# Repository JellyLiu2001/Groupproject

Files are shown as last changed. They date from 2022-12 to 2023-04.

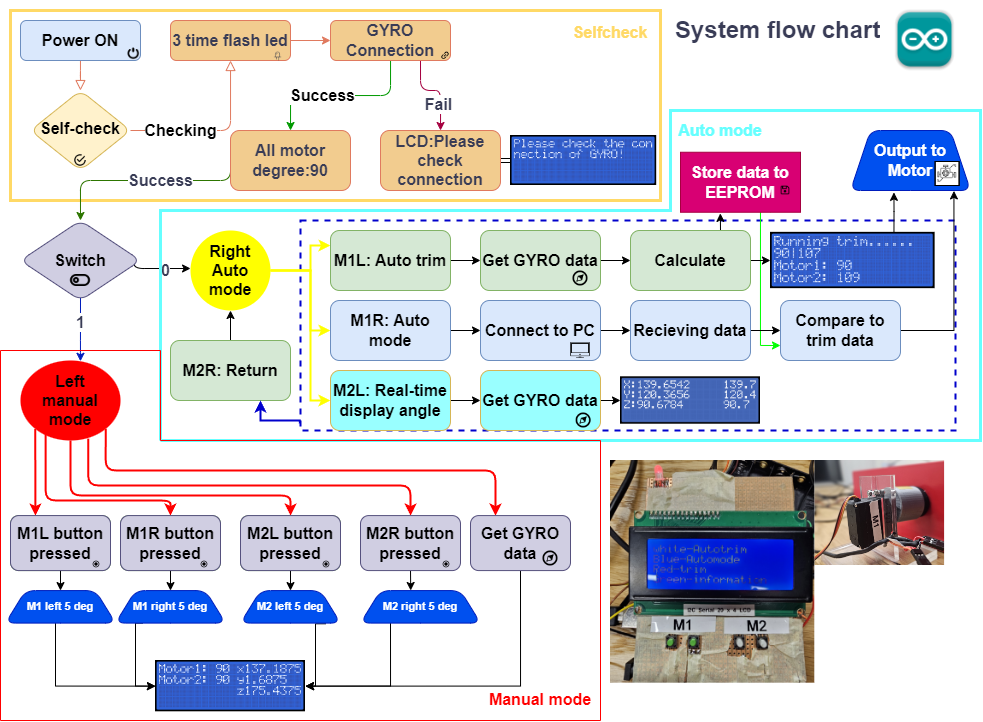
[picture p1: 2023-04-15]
Report-ab20328/flow chart.png

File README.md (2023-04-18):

# Groupproject
ab20328-Jelly Jinzhe Liu
## Abstract

This report is based on a group project of selecting and configuring motor and processor, designing a circuit, writing code, and discussing its feasibility.	
The part of this report on the group project is to discuss the feasibility of the motor and processor, using the result to choose the motor and integrated it into the maze. The processor needs to choose the model, design the circuits, and write the code. Also, when the image processing is finished, it must use the same port the processor provided. 

## Introduction
In the hardware part, the main function is using the motor to drive two knobs in the maze, which can control the pitch and roll. This function is leading the ball running in the guided route in case of not dropping the hole and to the destination. It uses two servo motors to drive the maze by connecting to Arduino Mega. when the system turns on, Arduino will do a self-check to make sure every component is connected and working well. Table 1 shows its component for users. 
After self-check, the user can choose two modes: auto mode and manual mode. It also includes auto trim, connect to pc and degree in auto mode. 
The benefit of this plan is to keep the original appearance and function of the maze, so people can still use it like the product itself. 

## Direction
Machines should always serve humans. A useful product not only has perfect hardware but also has good practicality. It is important to choose how to use it. 
In our design, the first task or main function is the connection to the PC and the use of two servos to drive the maze. Every part should give a visualization to the user to let them know what the system is doing, and easy to check errors. One of the problems is that the user will place the maze on different planes, therefore, the angle of the maze will change concerning the horizontal plane. In our design, we want it can be auto trim, which is to design a system that the user does not need to trim and still can get horizon. 
Config.h
Library	It is a set of pre-written code files designed to solve specific problems or provide specific functions, and developers can import them into their own code for use. A library can contain functions, variables, objects, etc., along with their associated header files, source code, and other resources.
adaFruint_sensor	Many small embedded systems exist to collect data from sensors, analyse the data, and either take an appropriate action or send that sensor data to another system for processing. (Adafruit, 2023)




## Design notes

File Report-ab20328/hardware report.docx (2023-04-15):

Jelly Jinzhe Liu – AB20328

AB20328@bristol.ac.uk

Mian contribution: Hardware

A clear report showing my contribution to the group project

Group Project 3 2022

Individual report

/

# Abstract

This report is based on a group project of selecting and configuring motor and processor, designing a circuit, writing code, and discussing its feasibility.

The part of this report on the group project is to discuss the feasibility of the motor and processor, using the result to choose the motor and integrated it into the maze. The processor needs to choose the model, design the circuits, and write the code. Also, when the image processing is finished, it must use the same port the processor provided.

# Introduction

Table 1 User’s component in Arduino mega
NAME | NUMBER
Button | 4
Switch | 1
LCD screen | 1
GYRO | 1
Full-colour LED | 1

In the hardware part, the main function is using the motor to drive two knobs in the maze, which can control the pitch and roll. This function is leading the ball running in the guided route in case of not dropping the hole and to the destination. It uses two servo motors to drive the maze by connecting to Arduino Mega. when the system turns on, Arduino will do a self-check to make sure every component is connected and working well. Table 1 shows its component for users.

After self-check, the user can choose two modes: auto mode and manual mode. It also includes auto trim, connect to pc and degree in auto mode.

The benefit of this plan is to keep the original appearance and function of the maze, so people can still use it like the product itself.

# Direction

Machines should always serve humans. A useful product not only has perfect hardware but also has good practicality. It is important to choose how to use it.

In our design, the first task or main function is the connection to the PC and the use of two servos to drive the maze. Every part should give a visualization to the user to let them know what the system is doing, and easy to check errors. One of the problems is that the user will place the maze on different planes, therefore, the angle of the maze will change concerning the horizontal plane. In our design, we want it can be auto trim, which is to design a system that the user does not need to trim and still can get horizon.

# Hypothesis/ Feasibility

## Motor/actuator

In this part, our main theme is trying to keep the product itself. Thus, we choose to use two knobs controlled by a servo motor.

The servo motor is a positional (angle) servo driver, which is suitable for the closed-loop control execution module that needs to change and maintain the angle constantly. In our project, we can be adjusting and monitor the angle by PWM. Compared to other motors, the servo motor has good stability and quick response. Therefore, I can control the knob fast and precisely.

Operating Speed: 60/0.15 degree/second (No Load @ 6.0V)

Stall Torque: 9.4 kg/cm @ 4.8V / Stall Torque: 11 kg/cm @ 6V

Running Current: 500mA-900mA @ 6V

Stall Current 2.5A @ 6v

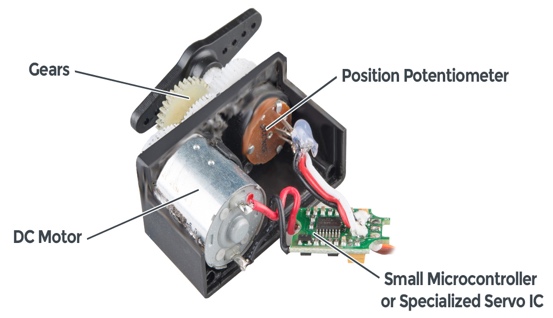
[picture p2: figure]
Servos Explained - SparkFun Electronics

Figure 1 - the structure of servo motor | Table 2 MG996R 180° servo motor features. (MG996R Servo Motor, 2019)

Figure 1 shows servo motor uses gears, which causes it can be high torque, and I can set the degree directly by using its potentiometer. In 6V, the torque can be 11kg/cm (Figure 1 - the structure of servo motor | Table 2 MG996R 180° servo motor features. (MG996R Servo Motor, 2019)). according to my measurement, the force of the knob is _____, Which is enough for our project. I did not choose a small servo motor, such as SG92R, So, I want to give some redundancy to prevent subsequent processes from adding weight.

## Processor

The processor’s main function is to drive two motors. It also should take part in connecting different hardware and transferring information. As I discussed with my group member, we will use the computer as the main computing service. Meanwhile, the hardware parts also need the ability to do some light work.

In this project, there are plenty of MCU (Microcontrollers unit) in the market, such as Arduino, Raspberry Pi and so on. As we considered, MCU does not participate in complex calculations. Thus, there is no need to use Raspberry Pi. Moreover, Arduino is our first choice.

### Choosing Arduino

According to the official website, Arduino is an open-source electric platform based on hardware and software. (Arduino, 2018) It can be receiving the input signal and output signal to control the servo motor or other devices, which is easy to use in our project.

In Arduino, there are a few models for users to choose from, such as Uno and Mega.

| Uno | Mega2560
Clock speed | 16MHz | 16MHz
Flash memory | 32kB | 256kB
EEPROM | 1 | 4
SRAM | 2 | 8
Voltage | 5v | 5v
I/O pins | 14 | 54
I/O pins with PWM | 6 | 15
Analog pins | 6 | 16

Table 3 The comparison between Arduino Uno and Mega

From Table 3, I compared two popular Arduino controllers, which clearly describe that Arduino Mega is better than Uno. Mega has bigger flash memory than Uno, which is it can store more data. Also, it has fifty-four pin that allows me to insert more hardware. Overall, I decided to choose Mega as our processor. In Arduino, there is another feature call EEPROM(Electrically Erasable Programmable Read-Only Memory). This feature can allow Arduino retain data even after a power outage.

## Components

### GYRO

In this project, we will make sure the maze should put it in horizontal. Thus, I decided to install a GYRO as a sensor to collect the data and analyse to data to balance the maze’s surface. I go to the universities tech hub; they have the GYRO(BNO005) to achieve what I need.

### Screen

To display the information, it is necessary to install a monitor. In Tech Hub, they give me to 2002 screen which can display forty characters that can carry more information instead of using the transition effect of the small screen.

## Mode/Function

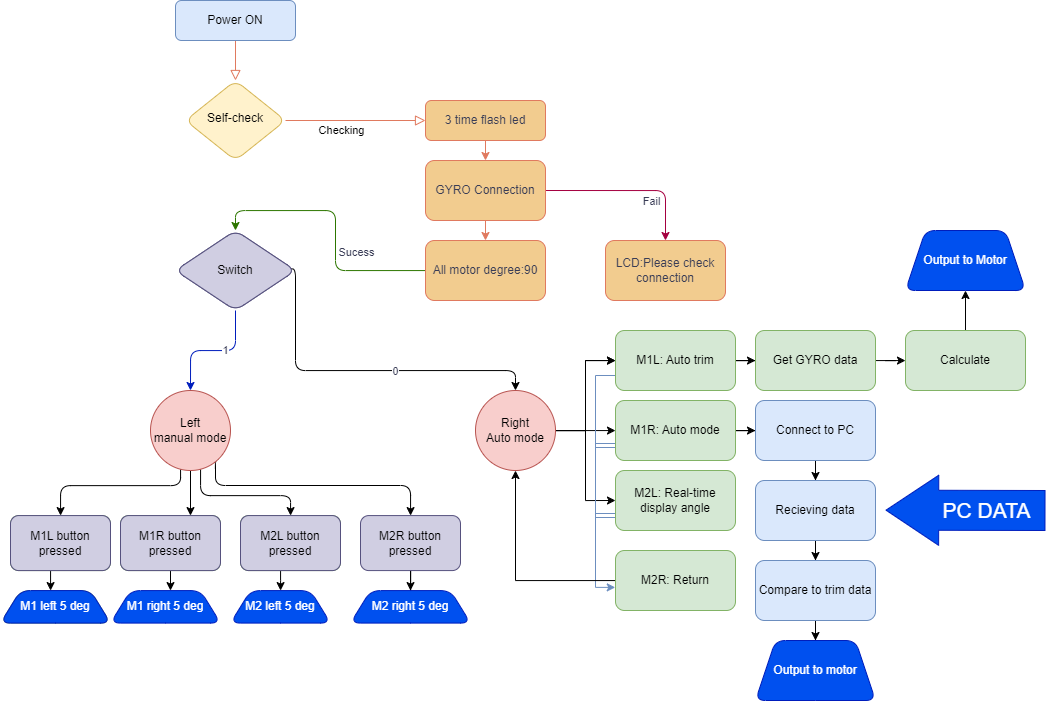
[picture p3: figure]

Figure 2 - The function of the hardware

Figure 2 shows the function that I designed for this project. There are three main functions describe below.

### Selfcheck

The selfcheck function can check if every component is connected. For GYRO, it can be checked through the screen. It will display a message if the GYRO is disconnected by Arduino. For led, I used full colour led. In this function, it will flash three channel to check it by visual inspection. If the colour is not white, that means one output is disconnected. For motor, they will turn to 90 degrees to check if it is working.

### Manual mode

By turning the switch, it can be change to manual mode. Manual adjustment can be used for users to manually control the angle of the servo through buttons. It also can control the pitch and roll and used in some situation such as testing and playing.

### Auto mode

In auto mode, there are a few modes user can choose including auto trim, shows degree and connect to pc.

- In auto trim, the maze can automatically balance by the data of GYRO. It can be easily for user without trim it manually. The GYRO should be installed in the maze, it can read the data and transmit to Arduino. There will be a judgment function to analyse the degree. If the degree is lower or higher than set value, then Arduino will calculate the adjustment value and output to motor to realise the trim function.
- Real time display mode can display the axis on screen in real time. So, user can check if it is horizonal and vertical to record the data.
- Connection to PC is using the camera above to capture the image and transmission to PC, PC will give the motor data to Arduino. And Arduino will drive the motor and display the information.

# Design and connection

After determining the pattern, the next step is the design. In this project, it needs to design the circuits and case to make it smaller and smarter. In order to look more like an integrated, we need to make all the components into a whole which needs to connect all components (Table 1).

Firstly, I made a simulation by using Tinker CAD. This software can simulation the basic Arduino and components. It will increase the speed of testing without using physical test on breadboard. The Figure 3 shows the circuits design and simulation.

In this simulation, each component should connect to the digital port in Arduino. In button and switch, they have similar features, which is the closure of the switch to generates a signal. Thus, it should be powered by 5v and put a resistor and signal wire in parallel to avoid short circuits. So, it should get power from the Arduino 5V into the switch/button and connect the signal wire to Arduino digital port. Then, make a resistor in parallel to GND.

In motor connection, the SN996R has three ports which is positive, negative and PWM signal. It just needs to connect to each function. During operation, I found that the servo motor is sometimes out of control. After checking, I found that although the motor can be powered by 5v, other components cannot work properly due to the excessive current demand of the servo motor. Thus, it should be powered by external supply. There are one thing needs to notice that when it uses external power supply, the motor and the Arduino needs to share the same reference voltage which is connect the GND together (green circle in Figure 3). Otherwise, it might cause unstable of the motor, further be damaged.

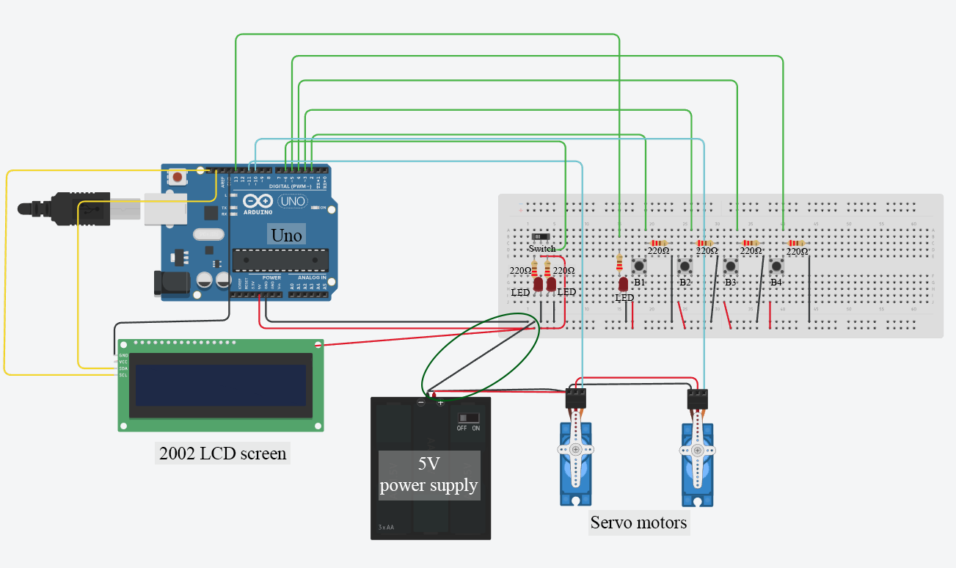
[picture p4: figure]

Figure 3 - The simulation of the circuits

After the simulation, I used the laser cut board to make a table and put all component in the table. (Figure 4)

It works well, but it does not meet the needs of portability, so it is necessary to use PCB. PCB is a printed circuit board that can substrate for connection of electronic components and circuit conduction. It should design the wire first and soldering all the components into the PCB. Because all wire will cover in the PCB, thus it can very small and achieve the same function. In Figure 5, it shows the design of this project’s PCB. It can be installed just above the Arduino mega, which is like an extension board.

In fact, this kind of board has never been used by me, because in the later inspection, I found that the production cycle of manufacturers in the market is relatively long, and the cost of independent production is expensive. It is still a good attempt.

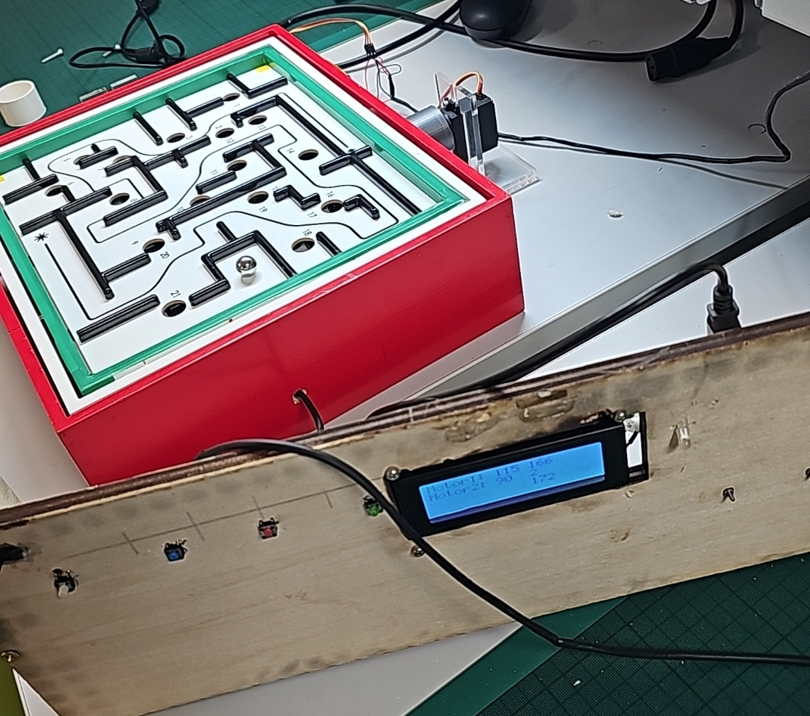
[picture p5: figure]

Figure 4 - The first model

Finally, the electric lab of university gives me a coper board, which allows me to solder the components and wires in it. After I solder it complete as same as the simulation one, here comes this

It can be also insert to the Arduino and it to use, just a little bigger than normal PCB. The two wires are connecting to the GYRO and MOTOR.

For the motor design, after I discussed to my group member, we have better idea. Thus, Yanbo is responsible of 3D design and print and Chenghao did the motor stand as they good at.

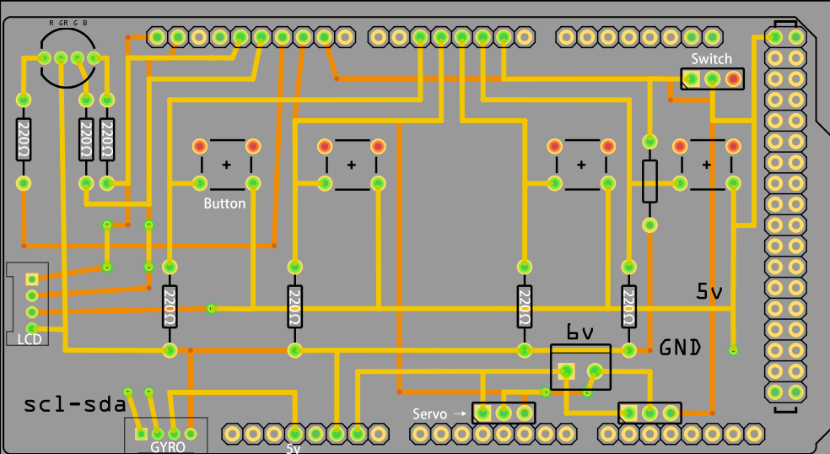
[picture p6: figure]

Figure 5 - PCB design

# Code

In the code part, I divided the code of the entire project into eight files.

Group Project.ino | Config.h | Init_setup.ino | Gyro.ino | Selfcheck.ino | Transfer.ino | Switch_value_manual.ino | Switch_value_mode.ino

### Group Project.ino

  - In this file, it included the basic running code. This code can be used to run all the functions.

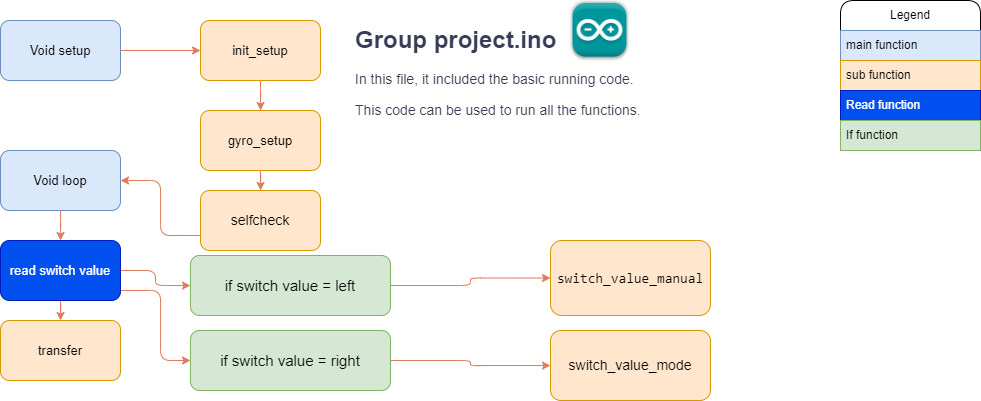
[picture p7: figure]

Figure 6 - The structure of Group Project.ino

  - In void setup function, it only runs one time when the Arduino turned on. In this program, it will run three sub function that included init_setup, gyro_setup, selfcheck.
  - In void loop function, it contains all the programs. In this program, the main function is checking the switch value. If the switch value is turning left, which means the circuits is cut off. Then, the digital pin cannot receive any voltage level, which is zero. In the same way, the switch will change to one, if the switch is turned to right. All in all, the value can be changed by turning left and right so that Arduino can detect and make actions.

### Config.h

  - In Arduino, config.h is a head file that usually define each pin and libraries.

Config.h
Library | It is a set of pre-written code files designed to solve specific problems or provide specific functions, and developers can import them into their own code for use. A library can contain functions, variables, objects, etc., along with their associated header files, source code, and other resources.
adaFruint_sensor | Many small embedded systems exist to collect data from sensors, analyse the data, and either take an appropriate action or send that sensor data to another system for processing. (Adafruit, 2023)
adaFruint_BNO055 | It is a library for the BNO055 model. This model is a GYRO that I install for our maze, it can provide the class for the hardware sensor that I can configure the sensor and read the data.
wire | It is a header file in Arduino that provides functions to communicate with I2C
LiquidCrystal_I2C | This library is to use the lcd screen on the Arduino by I2C connection.
Servo | Servo library is combined servo function that I can config it easily.
Global variable | Is to declare all value in Arduino.
LED | Declare each color’s pin.
Button | Declare each button’s pin
Servo motor | Declare the servo’s pin, degrees and set the current and past degree.
Screen | Declare the screen’s I2C address and display’s size.
GYRO | Declare the reference degree and other calculation degree name.
PC | Declare the Transfer status that used for PC connection and the value for saving the data.
Function prototype | In this function, different function code can be decentralized storage in different function. It used to make the program clearly.
Transfer | Limit the angle of the motor to prevent damage due to excessive angles.
Selfcheck | Check each connection if it is working well.
gyro_setup | Setup the GYRO.
gryo_display | Used to display all angles from GYRO and has difference precision.
gryo_trim | Used to running auto trim.
init_setup | Define the baud rate, lcd, set led to output and servo. Then read the data from EEPROM.
switch_value_manual | Define the function for manual mode.
switch_value_mode | Define the function for auto mode.

### Gyro.ino

  - In this program, it contains all function of GYRO.

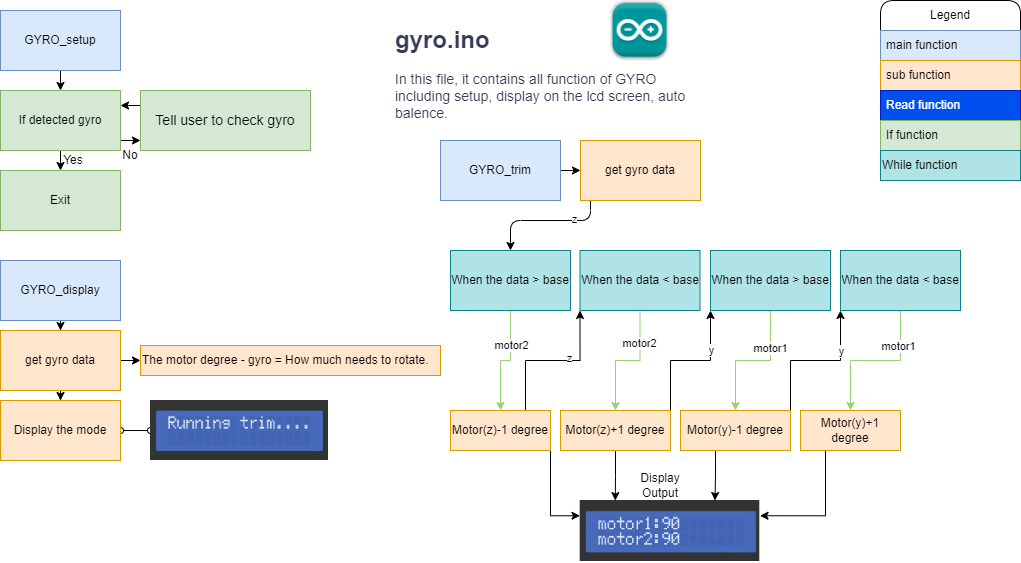
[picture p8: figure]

Figure 7 - The structure of gyro file.

  - In this file, it uses three void function to represent different gyro function.
  - For gyro_setup, this function is to define the gyro. The code bno.begin() is to check the if the gyro is connected to Arduino. If the gyro is connected, the Arduino will return 1 value to this code. On the opposite, the function will return 0, it will go to if function. In this function, the lcd screen will show the error message to user until the gyro is connected again and press reset button.
  - For gyro_display, this code describes the display function. In this program, there are some place needs to show different degrees. In this function, it can calculate how much degree needs motor rotate. This function is used for auto trim.
  - For gyro_trim, it used for auto trim as well. In this function, it can be auto balance by adjust two motors. Firstly, it will read gyro data. Next, there will be four WHILE function to determine the position of the maze board. These four functions can satisfy the angle in any case. Each while function is a loop, if the degree does not conform to the matches. The motor degree will increase or decrease one degree to check if it is match again. It will repeat the above steps until the adjusted angle matches the set angle. User can check its process by checking lcd display or led light.

### Selfcheck.ino

  - In the self-check function, it will run once when the Arduino is power on. At beginning, the lcd display shows welcome and self-test information to let user know what it is doing. Then, led will flash three times as stated above.

### Switch_value_manual.ino

  - This function allows user to adjust the motor degree manually by pressing four buttons.

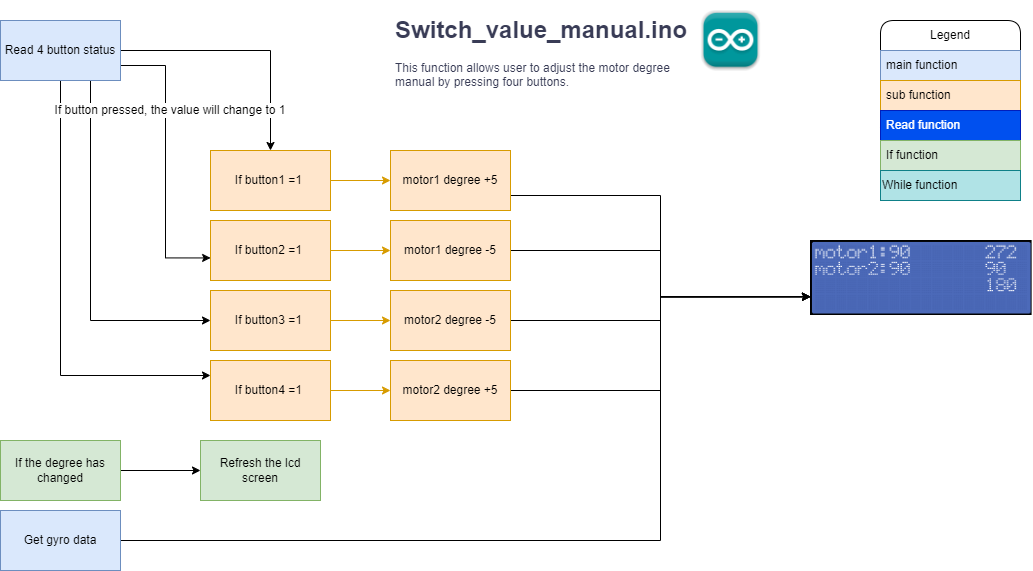
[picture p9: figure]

Figure 8 - The chart for manual mode

  - In this chart, I designed LCD refresh function. During each cycle, Arduino will compare the old motor data and new motor data. If new data does not same as old data, the lcd screen will run refresh function. if we insert lcd.clear() code to the normal code, the lcd screen will refresh all the time. Thus, user cannot see the screen clearly.
  - There are four If function that controlling the motor, if user pressed any buttons, the motor would increase or decrease the motor degree by each 5 deg.
  - In case of the readability, the gyro data will not only be showing on the display but also the following decimal part will be omitted, and only the integer will be displayed. The reason of this is to emphasize the main part. In most situation, user only needs to check integer degree. Thus, hiding decimal is necessary.

### Switch_value_mode.ino

  - In this mode, it contains the mode function that serves the maze.

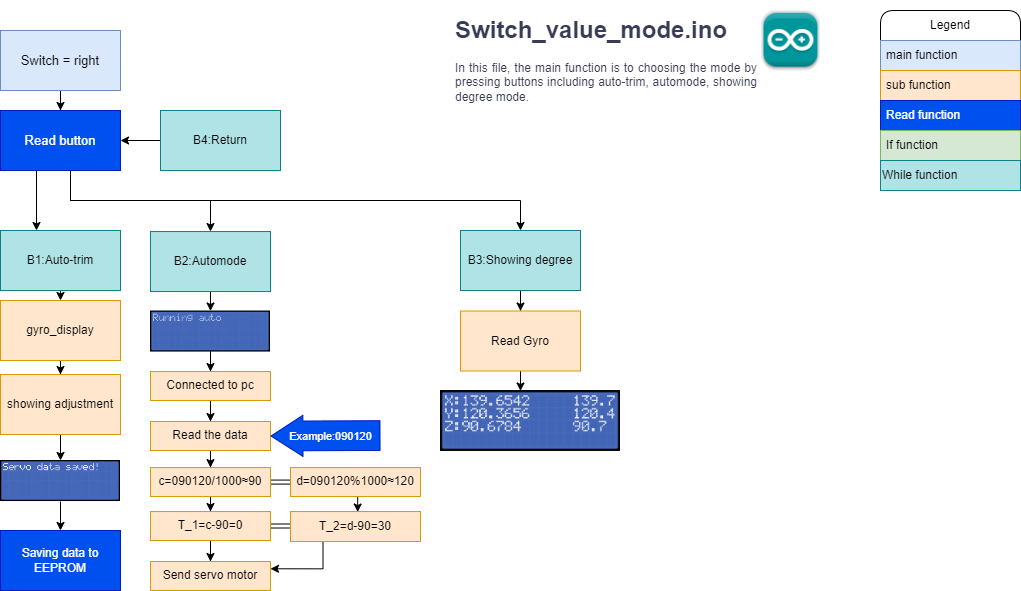
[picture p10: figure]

Figure 9 - The chart for switch_value_mode

  - From the Figure 9, this chart shows three functions based on gyro and pc.
  - The first mode is auto trim mode. In this while function, it uses two gyro functions as mentioned in gyro part. After finishing auto trim, the value of two motor degree will save to EEPROM and wait for next use.

Connecting to pc is one of the main functions. In this function, it needs to make a protocol to connect to pc. In Arduino, it gives a port that use to connect to pc by USB. It can not only send to data, but also receiving data. Serial.available() is used to detect the signal. This value will be greater than 0 if the data is transmitting. Thus, it can detect the message status. Every time when data is transmitting, it will enter a while function. Serial.parseInt() function will save all data from pc and named “num”.

For example: pc will send 090120 to Arduino, which means motor1=90deg, motor2=120deg. For motor1, the data(090120) will divide by 1000 =90.12. But we define motor1 is an integer, it only takes 90 as an integer. For motor2, it takes data’s remainder, so we can get 120. It needs to combine with GYRO that calculates the absolute degrees. In python, it presumes 90 degree is vertical and horizontal. Thus, the motor needs to rotate 90-90=0 in motor1 and 120-90=+30deg in motor2. To make sure the maze always be balance by putting on different table, we import the absolute vertical and horizontal data from EEPROM that we did auto trim before. So, the exact degree of motor is trim data +0 and trim data +30.

In order to prevent the computer from sending the same data twice to the Arduino, the user cannot judge whether the transmission is completed, a counting function is designed, which can switch back and forth between 1 and 2. So, user can easily check it by watching the display screen.

  - The real time display function also called showing degrees. In this mode, GYRO will collect data each second and drop it to display. On the left side, the data has 4 decimal numbers. On right side, the data only shows integer. This mode is used for testing the maze by checking faster high-precision data and clearer low-precision data.

# Conclusion

In summary, the hardware part of the maze system is designed to use two motor-driven knobs to control the pitch and roll of the maze. This feature enables the ball to follow the guided path and avoid falling into the hole as it moves towards its destination. The maze is controlled by two servo motors connected to an Arduino Mega board. After the system boots, the Arduino performs a self-test to make sure everything is connected and working properly.

The user can choose between two modes: automatic and manual, with additional features such as automatic trimming, connection to a PC and degrees in automatic mode. One of the main benefits of this program is that it retains the original look and functionality of the Maze, allowing people to use it like any other Maze product.

# Contribution

- Design and achieve the whole hardware part.
- Help image processing

# Advantages and Improvements

### Advantages

### Improvements

# Reference

Arduino. (2018, 02 05). arduino.cc. Retrieved from https://www.arduino.cc/en/Guide/Introduction

MG996R Servo Motor. (2019, 04 03). Retrieved from COMPONENTS101: https://components101.com/motors/mg996r-servo-motor-datasheet

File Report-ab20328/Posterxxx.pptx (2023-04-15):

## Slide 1

Group Research (Group C)
Jelly Jinzhe Liu – Hardware part
AB20328

Introduction

This project is to use the camera above the maze to capture the map of the maze and the ball for image recognition and path planning, and send the data to the motor connected to the maze to achieve automatic walking from the starting point to the end point without falling into the hole

Objective

In the hardware part, the main function is using the motor to drive two knobs in the maze, which can control the pitch and roll. This function is leading the ball running in the guided route in case of not dropping the hole and to the destination. It uses two servo motors to drive the maze by connecting to Arduino Mega. when the system turns on, Arduino will do a self-check to make sure every component is connected and working well.
After self-check, the user can choose two modes: auto mode and manual mode. It also includes auto trim, connect to pc and degree in auto mode. The benefit of this plan is to keep the original appearance and function of the maze, so people can still use it like the product itself.

Empirical Methodology

To use the motor as the maze driver, precise and fast motors are needed. Using servo motors is a good option to consider. Adding a gyro sensor can solve the problem of different ball speeds when the table is uneven. It's essential to establish simple, low-latency communication with the computer to reduce delay caused by turning the maze, which affects real-time performance. The manual mode is designed for users to adjust the maze angle themselves. The design mode selection function enables users or engineers to better use or debug the system.

Empirical Results

Reference

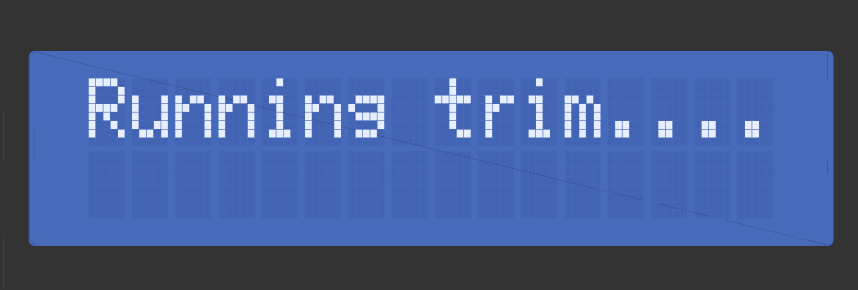
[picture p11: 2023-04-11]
Report-ab20328/running trim.png

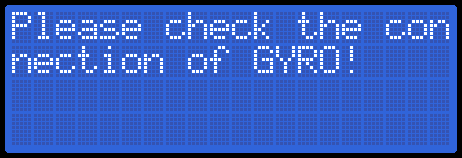
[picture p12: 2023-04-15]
Report-ab20328/screenshot (3).png

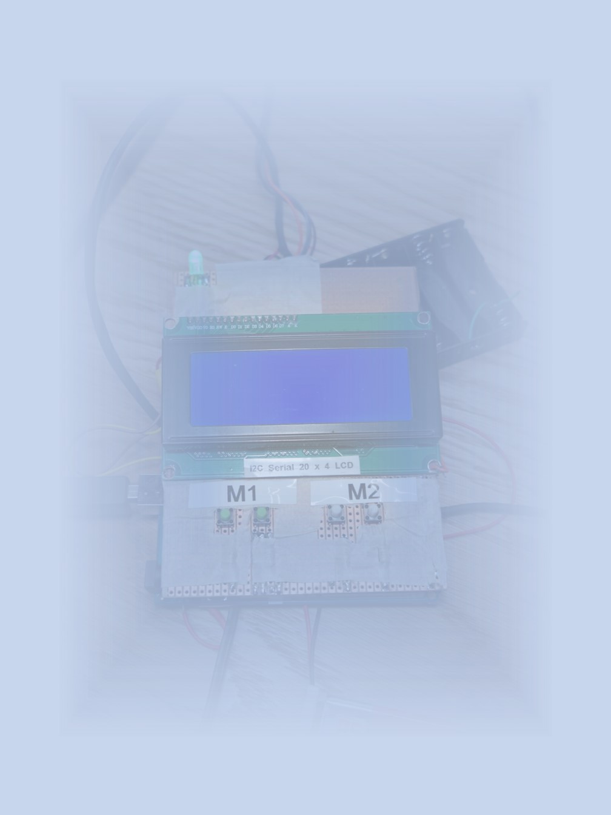
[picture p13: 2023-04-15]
Report-ab20328/poster.jpg

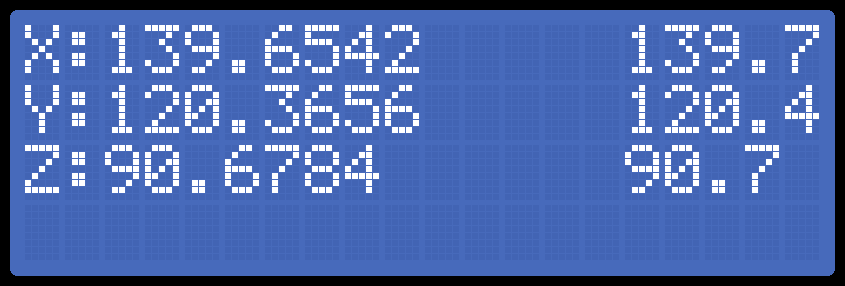
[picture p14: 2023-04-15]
Report-ab20328/screenshot (2).png

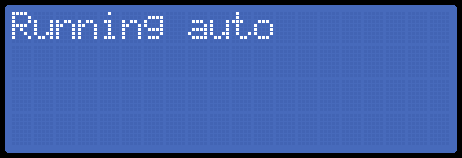
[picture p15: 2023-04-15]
Report-ab20328/screenshot (1).png

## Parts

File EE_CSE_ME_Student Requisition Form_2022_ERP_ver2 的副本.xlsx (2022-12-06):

Department of Electrical & Electronic Engineering
EE/CSE/MechElec PROJECT ORDER REQUISITION FORM (QB/MVB)
1: Your Details |  |  | 2: Supplier Details (one supplier per sheet please)
Your name: | Jinzhe Liu |  | Supplier Name: | Amazon
Your email ID: | ab20328 |  | Address/WWW Address (if having to use non-standard supplier) | https://www.amazon.co.uk/MMOBIEL-Airplane-Helicopter-Compatible-Raspberry/dp/B09BZTRSDP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
 |  |  |  | https://www.amazon.co.uk/dp/B08XXZ65H5?ref_=cm_sw_r_apan_dp_0DXW6884R2588CSK21W1
Project Supervisor: | WARR Paul |  |  | https://www.amazon.co.uk/ARDUINO-MEGA-2560-REV3-A000067/dp/B0046AMGW0?s=electronics
 |  |  |  | https://www.amazon.co.uk/gp/product/B01ICNT3HC/ref=ox_sc_act_title_2?smid=A1N4QYNYS6YJIC&psc=1
Date: | 19/11/2022
 |  |  | Telephone No: | /
 |  |  | email: | /
3: Your Order
NO.OF ITEMS | Order Code | ITEM DESCRIPTION |  |  | UNIT COST £ | SUB TOTAL £
2 | / | MMOBIEL Micro Servo Motor Kit MG995 55g 180° for RC Drone/Car/Airplane/Helicopter/Vehicles/Robots/Compatible with Arduino Projects and Raspberry Pi Incl. Screws and 4 Servo Arms |  |  | 8.99 | 17.98
1 | / | Webcam 1080P 60fps in Dual Noise Reduction Microphone Streaming Web Camera with Autofocus PC Web Cameras Compatible for Laptop Recording&Calling&Conference (black) |  |  | 46.98 | 46.98
1 | / | Arduino Mega 2560 REV3 [A000067] |  |  | 41.99 | 41.99
1 | B01ICNT3HC | Kuman Camera Module for Raspberry Pi 4 3 Model B B+ A+ 2 1 5MP 1080p OV5647 Sensor HD Video Webcam Night Vision Camera SC15 |  |  | 23.99 | 23.99
 |  |  |  |  |  | 0.00
 |  |  |  |  |  | 0.00
 |  |  |  |  |  | 0.00
 |  |  |  |  |  | 0.00
 |  |  |  |  |  | 0.00
 |  |  |  |  |  | 0.00
 |  |  |  |  |  | 0.00
 |  |  |  |  |  | 0.00
 |  |  |  |  |  | 0.00
 |  |  |  |  |  | 0.00
 |  |  |  |  |  | 0.00
 |  |  |  |  |  | 0.00
 |  |  |  |  |  | 0.00
 |  |  |  |  |  | 0.00
 |  |  |  |  |  | 0.00
 |  |  |  |  | Sub-Total £ | 130.94
 |  |  |  |  | VAT £ | 26.19
 |  |  |  |  | Total £ | 157.13
~ Once you have completed your order - please email this to your project supervisor who check your requirements and will then forward this on to the Technician for processing ~
4: Requisitioner Reference Codes (Technician use only) |  |  |  |  |  | Date
Notes: |  |  | CC | Punchout | Non-Punchout
 |  |  | Final Cost
 |  |  | Budget Code
 |  |  | ERP REQ No.
 |  |  | Date Received
 |  |  | ERP Purchase No.
 |  |  | ERP Receipt No.
 |  |  |  |  |  | Project Requisiton Form Ver8.0 eerjw 2022

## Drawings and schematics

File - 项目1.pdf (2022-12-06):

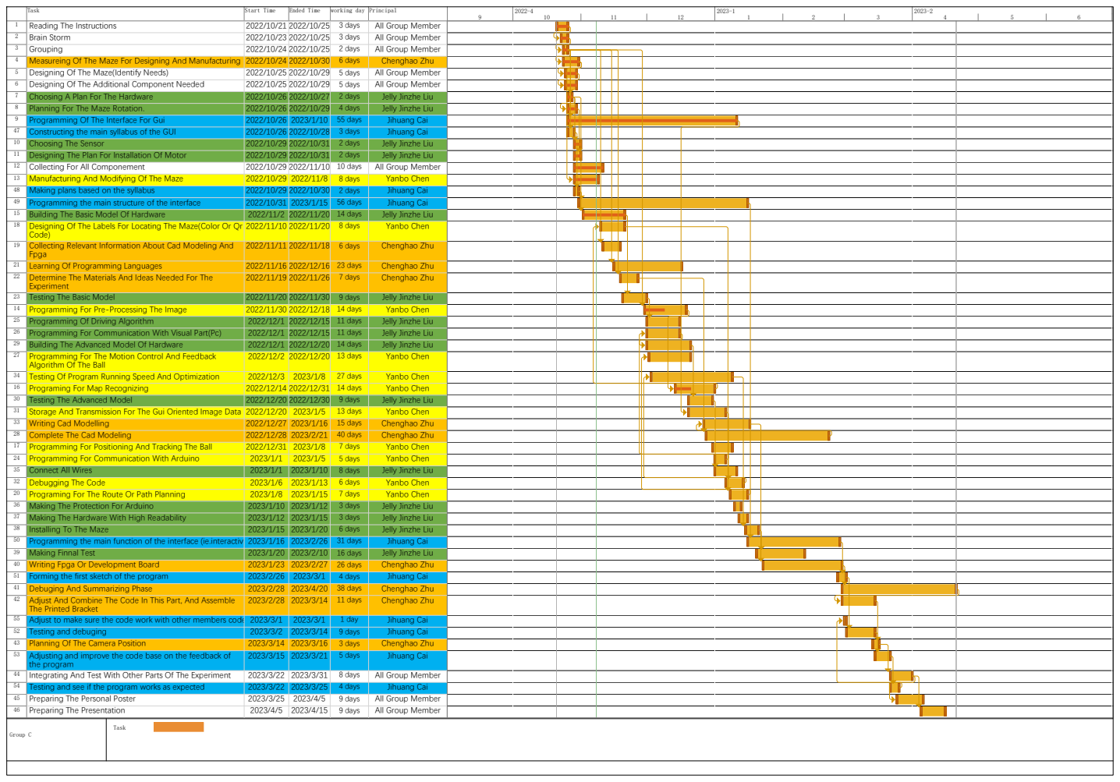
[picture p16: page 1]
Task; Start Time; Ended Time; working day; Principal; Reading The Instructions; 3 days; All Group Member; Brain Storm; Grouping; 2 days; Measureing Of The Maze For Designing And Manufacturing; 6 days; Chenghao Zhu; Designing Of The Maze(Identify Needs); 5 days; Designing Of The Additional Component Needed; Choosing A Plan For The Hardware; Jelly Jinzhe Liu; Planning For The Maze Rotation.; 4 days; Programming Of The Interface For Gui; 55 days; Jihuang Cai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

Code)
Fpga
Experiment
Algorithm Of The Ball
The Printed Bracket
the program

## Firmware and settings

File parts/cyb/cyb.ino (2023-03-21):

//Designed by Jelly Jinzhe Liu ab20328
/*
z:179-180--179
y:1-0--1
Led:13:12:11
Button&motor
Button:2:3:5:6
Switch:4
Motor:9:10
Screen:sda:scl 0x27
Motor:20度为0 - 190
*/
//---------gyro-----------
#include <Adafruit_Sensor.h>
#include <Adafruit_BNO055.h>
#include <utility/imumaths.h>
Adafruit_BNO055 bno = Adafruit_BNO055(55);
float base_y = 0.4375;  //设置基准角度
float base_z = 176.5;

//-----screen-----
#include <Wire.h>
#include <LiquidCrystal_I2C.h>
LiquidCrystal_I2C lcd_1(0x27, 20, 3);  // set the LCD address to 0x27 for a 16 chars and 2 line display
int lcd = 1;

//---舵机---
#include <Servo.h>
int pre_deg_c, current_c = 0;
int current_d, pre_deg_d = 0;
Servo servo_1;  //声明舵机
Servo servo_2;  //声明舵机2
//校准舵机角度
long num = 0;
int c = 90;  //舵机20为0度
int d = 90;
int i;
//---led---
int green = 11;
int blue = 12;
int red = 13;
int led_delay = 100;
//---按钮---
int switch_value = 0;                                                        //声明变量，用来存储按钮返回值HIGH或者LOW；
const int SWITCH = 4;                                                        //声明变量，开关接在第6针脚；
int BUTTON_VALUE_1_B, BUTTON_VALUE_2_W, BUTTON_VALUE_3_G, BUTTON_VALUE_4_R;  //声明按键状态
                                                                             //motor1
int BUTTON1_M1_BLUE = 5;                                                     //blue
int BUTTON2_M1_WHITE = 6;                                                    //white
                                                                             //motor2
int BUTTON1_M2_GREEN = 2;                                                    //green
int BUTTON2_M2_RED = 3;                                                      //red

//配平角度
int ydeg, zdeg;
int y_balence, z_balence;
//-------------自动配平----------------
int connect = 1;  //发送信号1代表连接成功
int l[2];         //接收角度的列表
int stat = -1;    //在列表中0,1的切换
int trans = 0;    //传输监测
int degree_1[70];//定义舵机1的角度
int degree_2[70];//定义舵机2的角度
int deg_a,deg_b;//设置舵机循环范围
void setup() {
  Serial.begin(9600);
  lcd_1.init();  // initialize the lcd
  lcd_1.backlight();
  lcd_1.begin(20, 3);      //设定lcd行数
  pinMode(SWITCH, INPUT);  //定义SWTICH为输出模式；
  pinMode(green, OUTPUT);
  pinMode(blue, OUTPUT);
  pinMode(red, OUTPUT);
  servo_1.attach(9);   //设定舵机接口
  servo_2.attach(10);  //设定舵机接口
}


//------------------------------------------------------------------------------------------------------------------------------------
void loop(){
while (connect == 1)  //与其他建立连接
{

  digitalWrite(green, 1);
  while (Serial.available() > 0)  //当有信号的时候
  {
    trans = 1;
    stat = stat + 1;
    // l[stat] = Serial.parseInt();
    // c = l[0];  //等于第一次传回数据
    // d = l[1];  //等于第二次传回的数据
    num = Serial.parseInt();
    Serial.flush();
    // Serial.println(num);
    if (num != 0) {
      c = num / 1000;
      // Serial.println(c);
      d = num % 1000;
      // Serial.println(d);
      lcd_1.print(trans);
      lcd_1.setCursor(0, 0);
      lcd_1.clear();
      lcd_1.print("motor1:");
      lcd_1.print(c);
      lcd_1.print("|");
      lcd_1.setCursor(0, 1);
      lcd_1.print("motor2:");
      lcd_1.print(d);
      lcd_1.print("|");
      lcd_1.setCursor(0, 2);
      lcd_1.print("current status:");
      lcd_1.print(stat + 1);
      servo_1.write(c);  //改变舵机位置
      servo_2.write(d);
      if (stat == 1) { stat = -1; }
    }
  }
  trans = 0;
  lcd_1.setCursor(0, 3);
  lcd_1.print("Trans:");
  lcd_1.print(trans);
}
}

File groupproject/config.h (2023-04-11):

//Designed by Jelly Jinzhe Liu ab20328
/*
z:179-180--179
y:1-0--1
Led:13:12:11
Button&motor
Button:2:3:5:6
Switch:4
Motor:9:10
Screen:sda:scl 0x27
Motor:20 degrees = 0 - 190
*/
//EEPROM

//---------gyro-----------
#include <Adafruit_Sensor.h>
#include <Adafruit_BNO055.h>
#include <utility/imumaths.h>
Adafruit_BNO055 bno = Adafruit_BNO055(55);
float base_y = -0.375;  // Set the base angle for the gyroscope
float base_z = 175.937;

//-----screen-----
#include <Wire.h>
#include <LiquidCrystal_I2C.h>
LiquidCrystal_I2C lcd_1(0x27, 20, 3);  // Set the LCD address to 0x27 for a 20-character and 4-line display
int lcd = 1;

//---servo---
#include <Servo.h>
int pre_deg_c, current_c = 0;  // Compare the current data with the previous data on the screen and refresh the screen if there is a change
int current_d, pre_deg_d = 0;
Servo servo_1;  // Declare servo 1
Servo servo_2;  // Declare servo 2
// Calibrate the servo angle
long num = 0;
int c = 90;  // Servo 20 degrees = 0 degrees
int d = 90;
int i;  //used for "for" function
//---led---
int green = 11;
int blue = 12;
int red = 13;
int led_delay = 100;
//---button---
int switch_value = 0;                                                        // Declare a variable to store the button return value HIGH or LOW;
const int SWITCH = 4;                                                        // Declare variable, switch connected to pin 6;
int BUTTON_VALUE_1_B, BUTTON_VALUE_2_W, BUTTON_VALUE_3_G, BUTTON_VALUE_4_R;  // Declare button status
// motor1
int BUTTON1_M1_BLUE = 5;   // Blue
int BUTTON2_M1_WHITE = 6;  // White
// motor2
int BUTTON1_M2_GREEN = 2;  // Green
int BUTTON2_M2_RED = 3;    // Red

// Balancing angle
int ydeg, zdeg;            // Store gyroscope input data
int y_balence, z_balence;  // Used to display the angle that needs to be balanced on the screen
//-------------Auto----------------PC
int connect = 1;   // Signal 1 means connection successful
int l[2];          // List of received angles
int stat = -1;     // Switch between 0 and 1 in the list
int trans = 0;     // Transmission monitoring
int deg_1, deg_2;  // Save the completed balancing data
int T_1, T_2 = 0;  // Compare the transmitted data with the balancing data
//-------------Pack-------
void transfer();             // Digital conversion
void selfcheck();            // Self-check
void gyro_setup();           // Gyroscope initialization
void gyro_display();         // Display gyroscope data on the screen
void gyro_trim();            // Gyroscope code when using auto-balancing
void init_setup();           // Initialize arduino code
void switch_value_manual();  // Manual mode
void switch_value_mode();    // Auto mode

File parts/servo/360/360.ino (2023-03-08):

// C++ code
//
/*
  Sweep

  by BARRAGAN <http://barraganstudio.com>
  This example code is in the public domain.

  modified 8 Nov 2013  by Scott Fitzgerald
  http://www.arduino.cc/en/Tutorial/Sweep
*/

#include <Servo.h>

int pos = 0;

Servo servo_9;
Servo servo_10;

void setup()
{
  servo_9.attach(9, 1000, 2500);
  servo_10.attach(13, 1000, 2500);
}

void loop()
{
  // sweep the servo from 0 to 180 degrees in steps
  // of 1 degrees
  for (pos = 20; pos <= 160; pos += 1) {
    // tell servo to go to position in variable 'pos'
    servo_9.write(pos);
    servo_10.write(pos);
    // wait 15 ms for servo to reach the position
    delay(15); // Wait for 15 millisecond(s)
  }
  for (pos = 160; pos >= 20; pos -= 1) {
    // tell servo to go to position in variable 'pos'
    servo_9.write(pos);
    servo_10.write(pos);
    // wait 15 ms for servo to reach the position
    delay(15); // Wait for 15 millisecond(s)
  }
}

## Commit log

2022-12-06 add screen and gyro
    [EE_CSE_ME_Student Requisition Form_2022_ERP_ver2 的副本.xlsx]
2023-01-26 add laser file
    [未标题-1.dwg]
2023-01-29 adding gyro
2023-02-07 adding pcb file
    [Untitled Sketch.fzz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]
2023-02-13 改进了舵机与绝对角度
2023-02-15 add servo data and clean the file from past
    [未标题-1.dwg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]
2023-02-18 deg tool finnish
    [data.xlsx]
2023-02-21 excel update
    [data.xlsx]
2023-02-27 adding communication
    [2deg.xlsx]
2023-03-05 change the button pin
2023-03-21 fixed the delay of connection
    [config.h, gyro.ino, switch_value_manual.ino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]
2023-03-21 add file for auto mode
    [Untitled Sketch.fzz]
2023-04-07 add translation
    [Untitled Sketch.fzz]
2023-04-11 add report file
    [2deg.xlsx, Untitled Sketch.fzz]
